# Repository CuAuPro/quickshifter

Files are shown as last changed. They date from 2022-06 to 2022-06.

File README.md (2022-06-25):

# Quickshifter
Quickshifter for motorcycle.

<!-- ABOUT THE PROJECT -->
## About The Project

Quickshifter for motorcycles based on measured force on gearbox. Implemented is pull-type quicksihfter but it allows, with small modifications, push-type also.

<p align="right">(<a href="#top">back to top</a>)</p>

### Built With

* [KiCad](https://www.kicad.org/)
* [STM32CubeIDE](https://www.st.com/en/development-tools/stm32cubeide.html)

<p align="right">(<a href="#top">back to top</a>)</p>

### Contents

* PCB
* Firmware

<p align="right">(<a href="#top">back to top</a>)</p>

<!-- CONTACT -->
## Contact

Kristjan Cuznar - [LinkedIn](https://www.linkedin.com/in/kristjan-cuznar/) - kristjancuznar0@gmail.com

Project Link: [https://github.com/CuAuPro/quickshifter)

<p align="right">(<a href="#top">back to top</a>)</p>

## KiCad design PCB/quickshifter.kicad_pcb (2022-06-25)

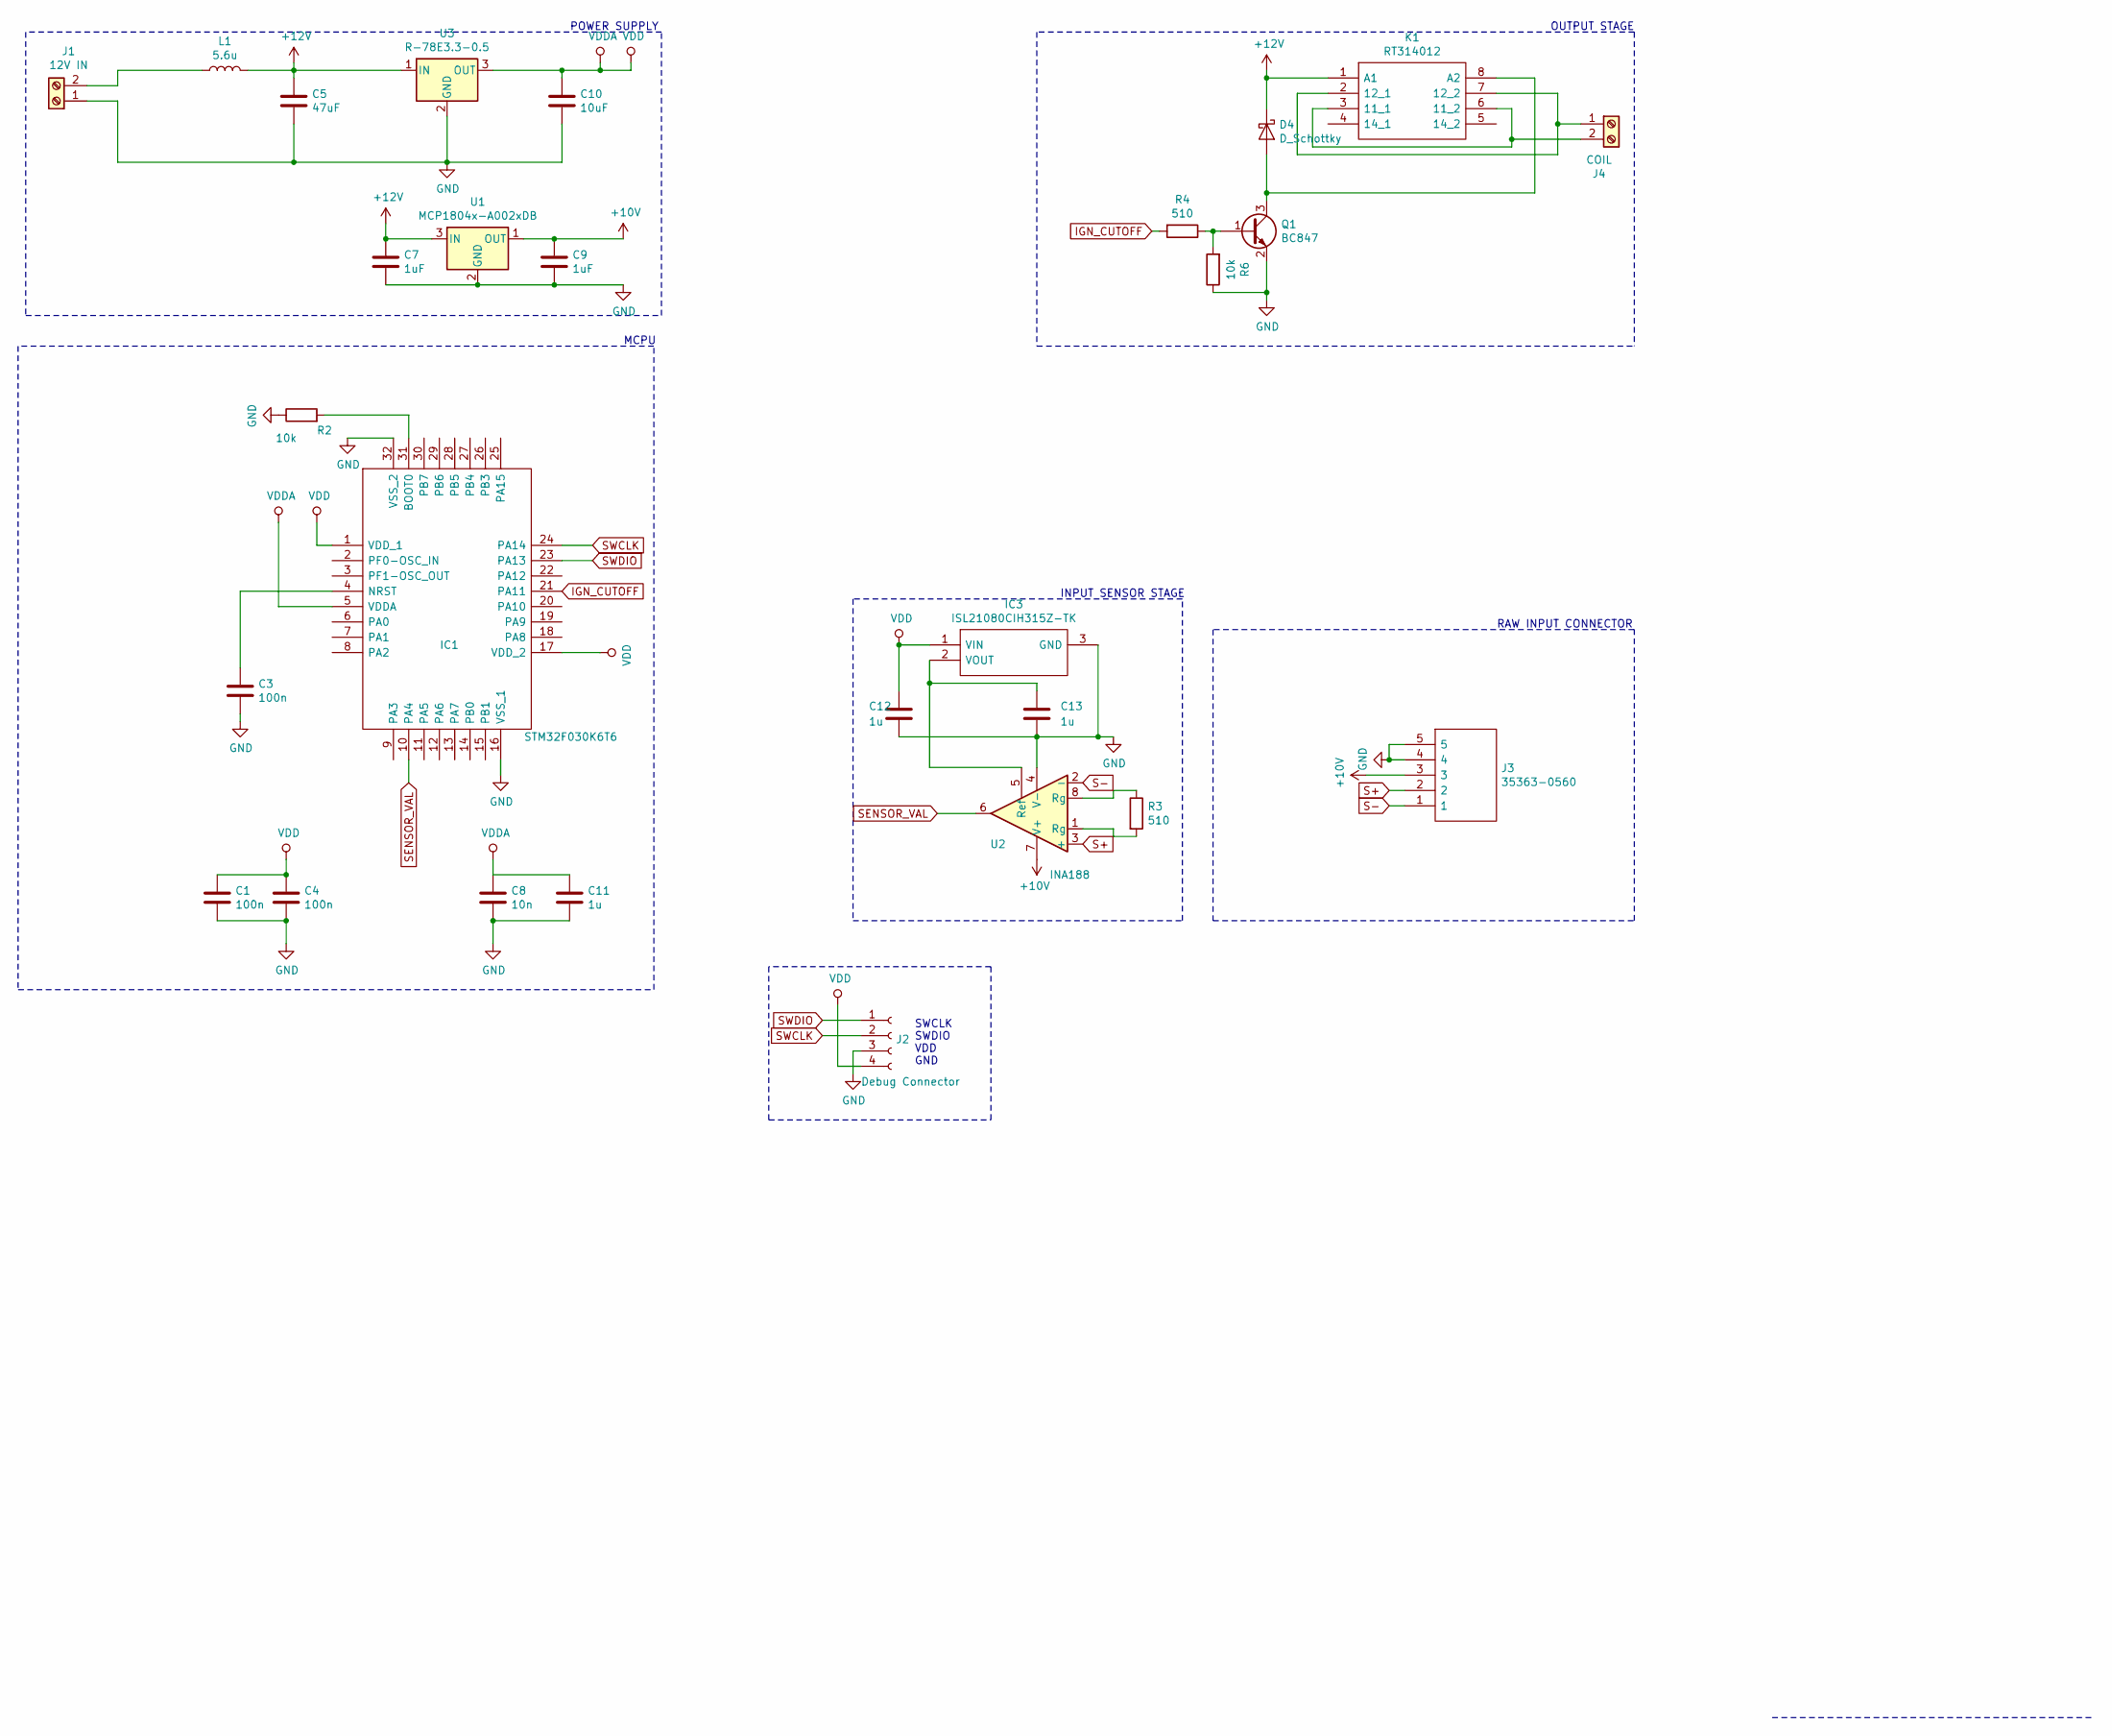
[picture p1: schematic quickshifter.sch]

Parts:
C1, C3, C4: 100n; C_0805_2012Metric_Pad1.18x1.45mm_HandSolder
C5: 47uF; C_0805_2012Metric_Pad1.18x1.45mm_HandSolder
C7, C9: 1uF; C_0805_2012Metric_Pad1.18x1.45mm_HandSolder
C8: 10n; C_0805_2012Metric_Pad1.18x1.45mm_HandSolder
C10: 10uF; C_0805_2012Metric_Pad1.18x1.45mm_HandSolder
C11, C12, C13: 1u; C_0805_2012Metric_Pad1.18x1.45mm_HandSolder
D4: D_Schottky; D_SOD-123; Farnell 2473410
IC1: STM32F030K6T6; QFP80P900X900X120-32N; Farnell 2432085
IC3: ISL21080CIH315Z-TK; SOT95P237X112-3N; Farnell 2358142
J1: 12V IN; SHDR2W80P0X350_1X2_840X920X720P
J2: Debug Connector; PinHeader_1x04_P2.54mm_Vertical
J3: 35363-0560; 353630560; Farnell 3107233
J4: COIL; SHDR2W80P0X350_1X2_840X920X720P
K1: RT314012; RT314005_2; Farnell 1629044
L1: 5.6u; L_0805_2012Metric_Pad1.15x1.40mm_HandSolder
Q1: BC847; SOT-23
R2, R6: 10k; R_0805_2012Metric_Pad1.20x1.40mm_HandSolder
R3, R4: 510; R_0805_2012Metric_Pad1.20x1.40mm_HandSolder
U1: MCP1804x-A002xDB; SOT-223-3_TabPin2
U2: INA188; SOIC-8_3.9x4.9mm_P1.27mm
U3: R-78E3.3-0.5; Converter_DCDC_RECOM_R-78E-0.5_THT

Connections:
+10V: C9.1, J3.3, U1.1 (OUT), U2.7 (V+)
+12V: C5.1, C7.1, D4.1 (K), K1.1 (A1), L1.2, U1.3 (IN), U3.1 (IN)
GND: C1.2, C3.2, C4.2, C5.2, C7.2, C8.2, C9.2, C10.2, C11.2, C12.2, C13.2, IC1.16 (VSS_1), IC1.32 (VSS_2), IC3.3 (GND), J1.1, J2.3, J3.4, J3.5, Q1.2 (E), R2.1, R6.1, U1.2 (GND), U2.4 (V-), U3.2 (GND)
IGN_CUTOFF: IC1.21 (PA11), R4.2
unnamed: C3.1, IC1.4 (NRST)
unnamed: C13.1, IC3.2 (VOUT), U2.5 (Ref)
unnamed: D4.2 (A), K1.8 (A2), Q1.3 (C)
unnamed: IC1.31 (BOOT0), R2.2
unnamed: J1.2, L1.1
unnamed: J4.1, K1.2 (12_1), K1.7 (12_2)
unnamed: J4.2, K1.3 (11_1), K1.6 (11_2)
unnamed: Q1.1 (B), R4.1, R6.2
unnamed: R3.1, U2.8 (Rg)
unnamed: R3.2, U2.1 (Rg)
S+: J3.2, U2.3 (+)
S-: J3.1, U2.2 (-)
SENSOR_VAL: IC1.10 (PA4), U2.6
SWCLK: IC1.24 (PA14), J2.2
SWDIO: IC1.23 (PA13), J2.1
VDD: C1.1, C4.1, C8.1, C10.1, C11.1, C12.1, IC1.1 (VDD_1), IC1.5 (VDDA), IC1.17 (VDD_2), IC3.1 (VIN), J2.4, U3.3 (OUT)

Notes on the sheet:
POWER SUPPLY
MCPU
SWCLK SWDIO VDD GND
RAW INPUT CONNECTOR
INPUT SENSOR STAGE
OUTPUT STAGE

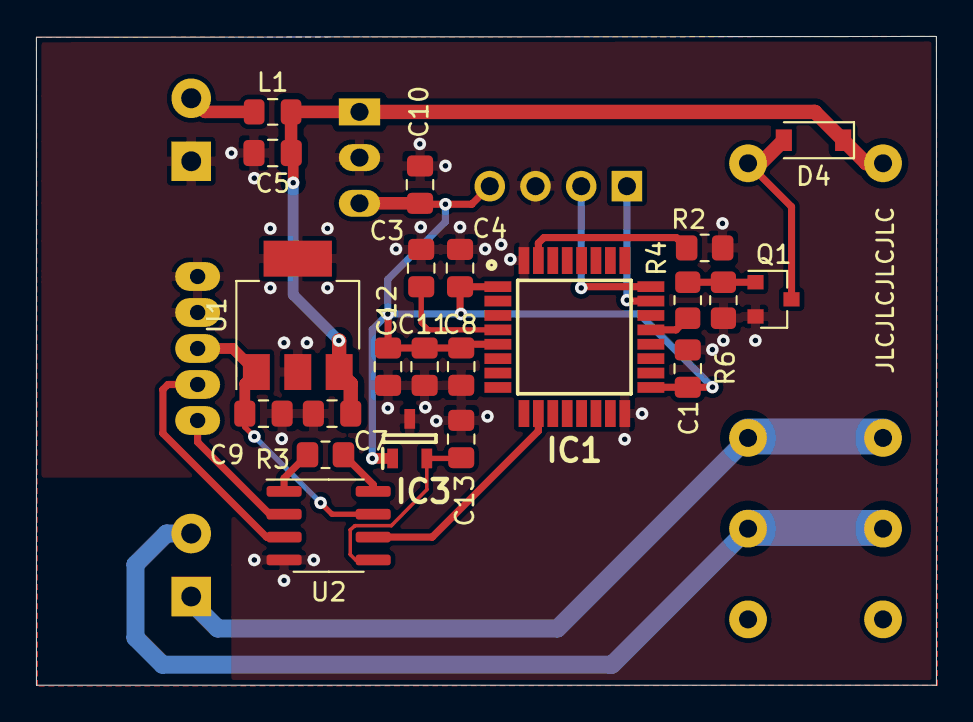
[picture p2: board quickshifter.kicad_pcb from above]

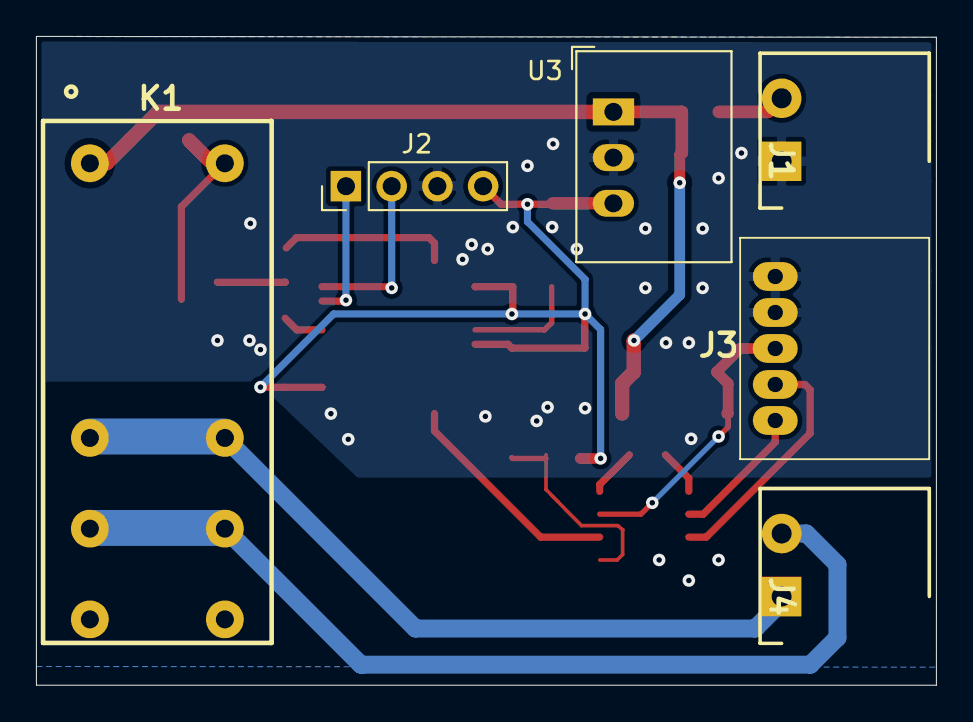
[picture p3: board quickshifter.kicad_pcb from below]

Board: 2 copper layers, 50.0 x 36.0 mm, 28 parts (6 on the bottom side), 20 nets.

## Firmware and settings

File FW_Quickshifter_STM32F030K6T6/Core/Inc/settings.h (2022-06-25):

/*
 * settings.h
 *
 *  Created on: Jul 7, 2020
 *      Author: Kristjan
 */

#ifndef INC_SETTINGS_H_
#define INC_SETTINGS_H_

#include "main.h"

#define DEFAULT_ADC_IDLE					1300	//ADC value
#define DEFAULT_SHIFT_FORCE					29		//kg
#define DEFAULT_TIME_IGNITION_OFF 			65		//ms
#define DEFAULT_TIME_NO_SENSING  			500		//ms
#define DEFAULT_SECOND_RUN_TIME_NO_SENSING  100		//ms

#define INST_AMP_GAIN						99
#define	ADC_VOLTAGE_REF						3300 	//mV

#define MAX_TIME_IGNITION_OFF				150		//ms
#define MAX_TIME_NO_SENSING					1000	//ms

#define POS_TIME_GEAR_1_2	0
#define POS_TIME_GEAR_2_3	1
#define POS_TIME_GEAR_3_4	2
#define POS_TIME_GEAR_4_5	3
#define POS_TIME_GEAR_5_6	4
#define POS_TIME_DEADTIME	5
#define POS_SHIFT_FORCE		6


typedef struct Settings{

	uint16_t CutoffTime;
	uint16_t deadtime;
	uint16_t ShiftForce;

} Settings_t;

typedef struct Control{

	uint16_t CutoffTime;
	uint16_t deadtime;
	int16_t ShiftForceADCLowTsh;
	int16_t ShiftForceADCHighTsh;

} Control_t;



#endif /* INC_SETTINGS_H_ */

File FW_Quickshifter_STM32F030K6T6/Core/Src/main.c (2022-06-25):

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
/* Includes ------------------------------------------------------------------*/
#include "main.h"
#include "adc.h"
#include "tim.h"
#include "gpio.h"

/* USER CODE BEGIN Includes */
#include "settings.h"
/* USER CODE END Includes */


/* USER CODE BEGIN PV */
volatile uint8_t flag_adc_high_treshold = 0;
volatile uint8_t flag_adc_low_treshold = 0;

Settings_t Settings;
Control_t Control;
uint16_t value;
/* USER CODE END PV */

void SystemClock_Config(void);
/**
  * @brief  The application entry point.
  * @retval int
  */
int main(void)
{
  /* USER CODE BEGIN 1 */
	Settings.CutoffTime = DEFAULT_TIME_IGNITION_OFF;
	Settings.deadtime = DEFAULT_TIME_NO_SENSING;
	Settings.ShiftForce = DEFAULT_SHIFT_FORCE;

	Control.CutoffTime = Settings.CutoffTime;
	Control.deadtime = Settings.deadtime;

	Control.ShiftForceADCHighTsh = (((float)INST_AMP_GAIN*(0.4189*(float)Settings.ShiftForce) - 2.9365) + DEFAULT_ADC_IDLE);
	Control.ShiftForceADCLowTsh  = (((float)INST_AMP_GAIN*(-0.4189*(float)Settings.ShiftForce) - 2.9365) + DEFAULT_ADC_IDLE);
	/* USER CODE END 1 */

	/* MCU Configuration--------------------------------------------------------*/

	/* Reset of all peripherals, Initializes the Flash interface and the Systick. */
	HAL_Init();

	/* Configure the system clock */
	SystemClock_Config();

	/* Initialize all configured peripherals */
	MX_GPIO_Init();
	MX_ADC_Init();
	MX_TIM1_Init();
	MX_TIM14_Init();
	MX_TIM16_Init();
	/* USER CODE BEGIN 2 */
	//HAL_GPIO_WritePin(ERROR_GPIO_Port, ERROR_Pin, RESET);
	HAL_GPIO_WritePin(IGN_CUTOFF_GPIO_Port, IGN_CUTOFF_Pin, RESET);

	//HAL_TIM_Base_Start(&htim1);
	HAL_TIM_Base_Start(&htim14);
	HAL_TIM_Base_Start(&htim16);
	HAL_ADC_Start_IT(&hadc);


	ADC1->CR |= ADC_CR_ADSTP;
	ADC1->IER &= ~(ADC_IER_AWD1IE);
	/* Shift the offset in function of the selected ADC resolution: Thresholds*/
	/* have to be left-aligned on bit 11, the LSB (right bits) are set to 0   */
	uint32_t tmpAWDHighThresholdShifted = ADC_AWD1THRESHOLD_SHIFT_RESOLUTION(&hadc, Control.ShiftForceADCHighTsh);
	uint32_t tmpAWDLowThresholdShifted = ADC_AWD1THRESHOLD_SHIFT_RESOLUTION(&hadc, Control.ShiftForceADCLowTsh);
	/* Set the high and low thresholds */
	hadc.Instance->TR &= ~(ADC_TR_HT | ADC_TR_LT);
	hadc.Instance->TR |= (ADC_TRX_HIGHTHRESHOLD(tmpAWDHighThresholdShifted) | tmpAWDLowThresholdShifted);
	/* Clear the ADC Analog watchdog flag (in case of left enabled by         */
	/* previous ADC operations) to be ready to use for HAL_ADC_IRQHandler()   */
	/* or HAL_ADC_PollForEvent().                                             */
	__HAL_ADC_CLEAR_FLAG(&hadc, ADC_IT_AWD);

	ADC1->IER |= (ADC_IER_AWD1IE);
	ADC1->CR |= ADC_CR_ADSTART;
  /* USER CODE END 2 */

  /* Infinite loop */
  /* USER CODE BEGIN WHILE */
	while (1)
	{
		//HAL_ADC_PollForConversion(&hadc, HAL_MAX_DELAY); //Testing force when shifting.
		//value = HAL_ADC_GetValue(&  hadc); //Testing force when shifting.

		/*/////////////////////////////////¸
	  PULL SYSTEM GOES BELOW MINIMUM LEVEL, PUSH SYSTEM GOES ABOVE MAXIMUM LEVEL!
		 *////////////////
    /* USER CODE END WHILE */

    /* USER CODE BEGIN 3 */
	}
  /* USER CODE END 3 */
}

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


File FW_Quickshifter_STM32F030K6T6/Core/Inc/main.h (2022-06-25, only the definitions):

#define SENSOR_Pin GPIO_PIN_4
#define SENSOR_GPIO_Port GPIOA
#define IGN_CUTOFF_Pin GPIO_PIN_11
#define IGN_CUTOFF_GPIO_Port GPIOA

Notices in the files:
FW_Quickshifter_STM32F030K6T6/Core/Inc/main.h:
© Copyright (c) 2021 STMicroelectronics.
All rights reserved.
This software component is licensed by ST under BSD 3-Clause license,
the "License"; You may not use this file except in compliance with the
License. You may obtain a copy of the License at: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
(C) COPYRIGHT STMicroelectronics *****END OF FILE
